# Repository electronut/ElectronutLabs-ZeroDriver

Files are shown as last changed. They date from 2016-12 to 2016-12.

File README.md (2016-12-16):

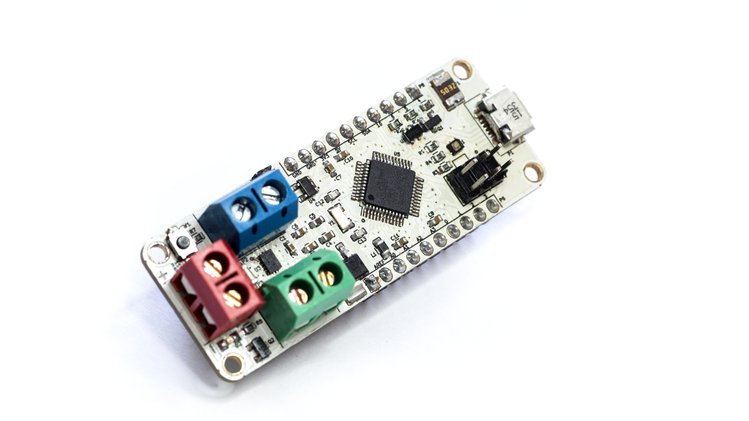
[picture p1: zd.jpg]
ZeroDriver


## What is it?

**ZeroDriver** is an Arduino Zero-compatible dual-motor driver board for robotics and mechatronics projects.

Robotics projects usually need two boards - a microcontroller board and a separate driver for the motors. ZeroDriver combines both in one for your convenience.

## Features & Specifications

* Atmel SAM D21 ARM Cortex-M0+ 48 MHz chip with 256KB Flash and 32KB SRAM
* Texas Instruments DRV8835 Dual Low-Voltage H-Bridge IC
* RGB LED
* Color coded terminal blocks for easy connectivity
* Standard 10-pin JTAG header broken out
* SPI header broken out
* Reverse polarity protection for power supply
* 12 V max power supply, 1.5 A current per H bridge
* Shipped with Arduino Zero bootloader for easy programming

## What can you do with it?

Well, depends on your imagination. :-)

But we do have some awesome demo projects - complete with code and design
information. Take a look at the [code](code/) directory.

## ZeroDriver Crowdfunding

We are currently trying to crowdfund the production of ZeroDriver at **Crowd Supply**.
Help us bring ZeroDriver to life!

https://www.crowdsupply.com/electronut-labs/zerodriver

## License

The following licenses apply to this work:

### Design Files

<br /><span xmlns:dct="http://purl.org/dc/terms/" property="dct:title">ZeroDriver</span> is licensed under a <a rel="license" href="http://creativecommons.org/licenses/by-sa/4.0/">Creative Commons Attribution-ShareAlike 4.0 International License</a>.<br />Based on a work at <a xmlns:dct="http://purl.org/dc/terms/" href="http://electronut.in/" rel="dct:source">http://electronut.in/</a>.

### Pin Diagram
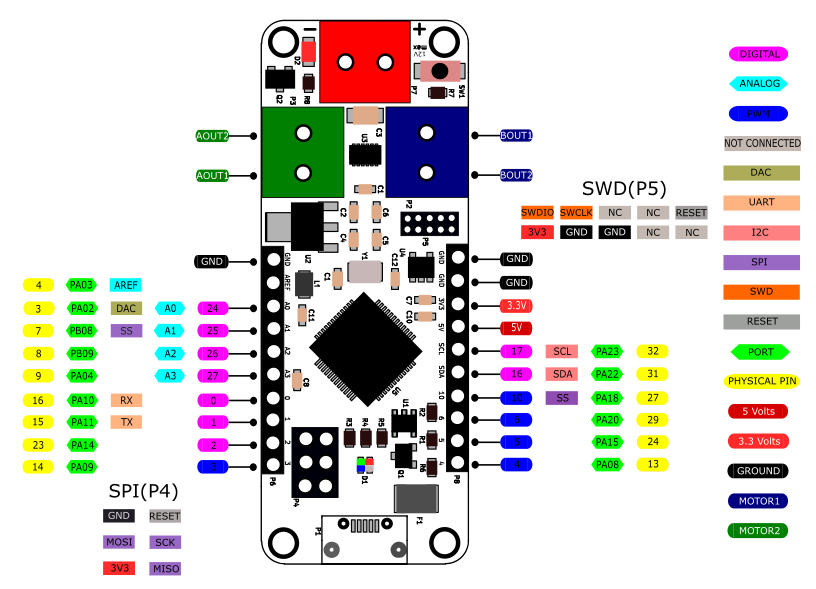
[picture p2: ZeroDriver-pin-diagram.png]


[Pinout](zerodriver-board-pinout.svg)
### Code

The MIT License (MIT)
Copyright (c) 2016 Electronut Labs (electronut.in)

Permission is hereby granted, free of charge, to any person obtaining a copy of this software and associated documentation files (the "Software"), to deal in the Software without restriction, including without limitation the rights to use, copy, modify, merge, publish, distribute, sublicense, and/or sell copies of the Software, and to permit persons to whom the Software is furnished to do so, subject to the following conditions:

The above copyright notice and this permission notice shall be included in all copies or substantial portions of the Software.

THE SOFTWARE IS PROVIDED "AS IS", WITHOUT WARRANTY OF ANY KIND, EXPRESS OR IMPLIED, INCLUDING BUT NOT LIMITED TO THE WARRANTIES OF MERCHANTABILITY, FITNESS FOR A PARTICULAR PURPOSE AND NONINFRINGEMENT. IN NO EVENT SHALL THE AUTHORS OR COPYRIGHT HOLDERS BE LIABLE FOR ANY CLAIM, DAMAGES OR OTHER LIABILITY, WHETHER IN AN ACTION OF CONTRACT, TORT OR OTHERWISE, ARISING FROM, OUT OF OR IN CONNECTION WITH THE SOFTWARE OR THE USE OR OTHER DEALINGS IN THE SOFTWARE.

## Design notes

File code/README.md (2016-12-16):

This directory consists of instructions and sample code for the examples developed using ZeroDriver.

**ZeroDriver-init** demonstrates the use of RGB LED and DRV8835 motor driver.

**Ultrasonic-bot** is an example of controlling DC motors i.e. their speed and direction using an ultrasonic sensor.

**Laser-step-test** demonstrates the ability of DC motors to generate various patterns using a laser pointer.

**Load-control** demonstrates the capability of DRV8835 is not only limited to control motors, but also in controlling and switching loads connected to the terminal blocks.

**stepper-iris** example explains the interfacing of a bipolar stepper motor with ZeroDriver. To make things interesting, an ultrasonic sensor controls the stepper motor to drive a mechanical iris.

**MeArm-joystick** demonstrates that MeArm - a robotic arm, can be controlled manually using two joysticks interfaced with the ZeroDriver.

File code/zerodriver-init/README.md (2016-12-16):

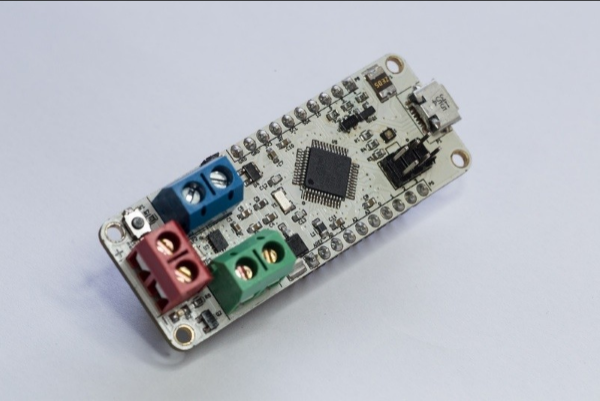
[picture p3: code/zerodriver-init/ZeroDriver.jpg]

#####ZeroDriver

Code to test RGB LED and DRV8835.

Plug in the USB to the ZeroDriver board and upload the code.

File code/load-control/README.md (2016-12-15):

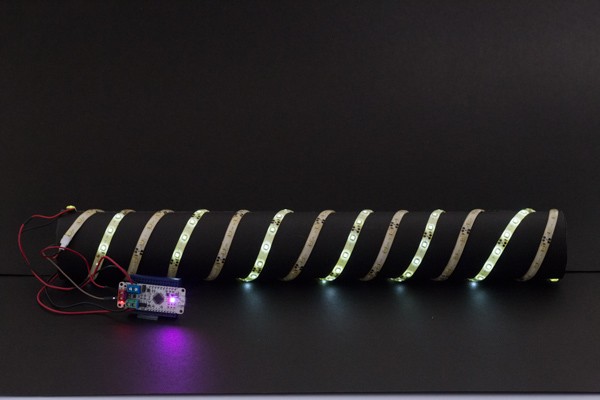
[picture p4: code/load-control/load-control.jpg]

#####LED strip control using H-bridges.

Two LED strips are connected to two H-bridges of the DRV8835. The RGB LED switches between _cyan_ and _magenta_ in accordance to the LED strip.

###Connections:
**LED strip** | **ZeroDriver**
--------- | ----------
VCC (LED strip 1) | AOUT1(+) Green terminal
GND (LED strip 1) | AOUT2(-) Green terminal
VCC (LED strip 2) | BOUT1(+) Blue terminal
GND (LED strip 2) | BOUT2(-) Blue terminal

_Note:_
Power ZeroDriver as per the ratings of the LED strip. Do not cross the max 12V input limit. Here, the board is powered with a 7.4V, 1300mAh LiPo battery.

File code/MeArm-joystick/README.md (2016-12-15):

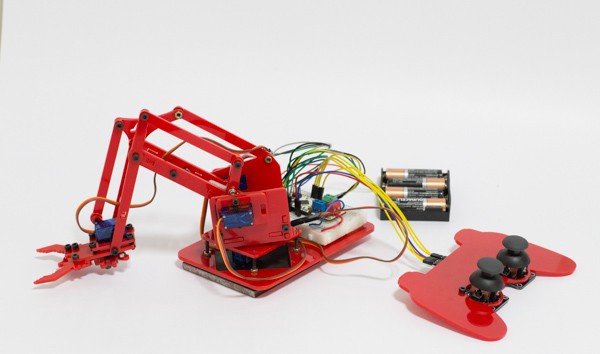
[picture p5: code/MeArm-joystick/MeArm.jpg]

#####Joystick interface with ZeroDriver to control [MeArm](https://mime.co.uk/products/mearm/).

The design files for MeARM are available at the link mentioned above. 
Design file for the joystick pad has been inuded in the repository.

###Connections:
**Joystick** | **ZeroDriver**
-------- | ----------
VCC | 3V3
XPOS (left joystick) | A0
YPOS (left joystick) | A1
XPOS (right joystick) | A2
YPOS (right joystick) | A3

**Servo Motors** | **ZeroDriver**
------------ | ----------
Base | 4
Left | 5
Right | 6
Claw | 10

_Note:_
Power the servo motors from 4 x AA batteries.

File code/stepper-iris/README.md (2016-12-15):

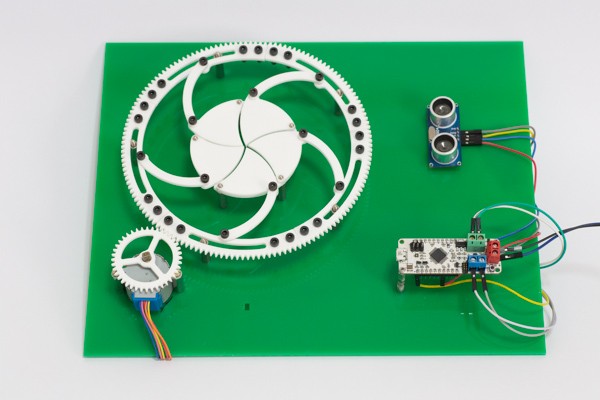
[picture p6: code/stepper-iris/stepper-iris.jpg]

#####Mechanical iris control using ultrasonic sensor and stepper motor

Controlling a mechanical iris using a stepper motor and an ultrasonic sensor. On detecting an object, the gear mounted stepper motor rotates, causing the iris to open. On removing the object, the iris is closed.

The iris design is based on a project - [Make an Awesome Mechanical Iris](http://makezine.com/projects/mechanical-iris/) by [Chris Schaie](http://makezine.com/author/chris-schaie/) The iris design has been modified for this project and included in the repository.

###Connections:
**HCSR-04** | **ZeroDriver**
------- | ----------
VCC | 5V
trigger | 2
echo | 4

**Stepper motor** | **ZeroDriver**
------------- | ----------
Blue | BOUT2(-) Blue terminal
Pink | AOUT2(-) Green terminal
Yellow | BOUT1(+) Blue terminal
Orange | AOUT(+) Green terminal

_Note:_

* The BYJ-48 is being used as a bipolar stepper motor in this demonstration. Do not connect the red wire of stepper motor. 
* HCSR-04 operates only when supplied with 5V. On powering with 3.3V, the sensor does not behave in a reliable manner. Naturally, on powering the sensor with 5V, the echo pin sends out 5V signals to the input pin 5 which can damage the board as the I/O pins are 3.3V compatible. Use a resistor divider network to generate 3.3V output from 5V echo signals.

###Reference:
https://itp.nyu.edu/physcomp/labs/motors-and-transistors/lab-controlling-a-stepper-motor-with-an-h-bridge/

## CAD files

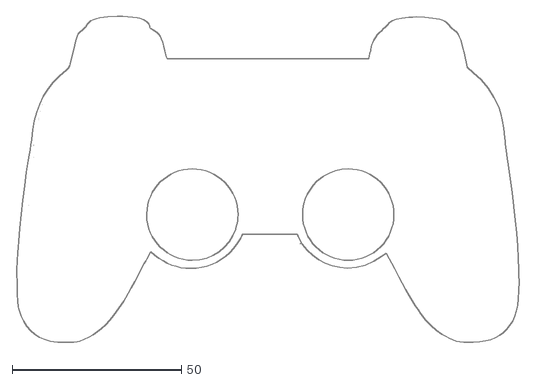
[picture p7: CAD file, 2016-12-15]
code/MeArm-joystick/Electronut-Labs-Joystick-board.dxf
148.8 x 96.6

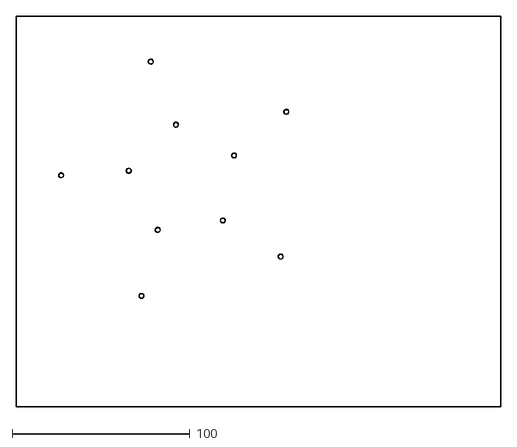
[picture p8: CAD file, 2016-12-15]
code/stepper-iris/Electronut-Labs-iris-frame.dxf
273.0 x 220.0

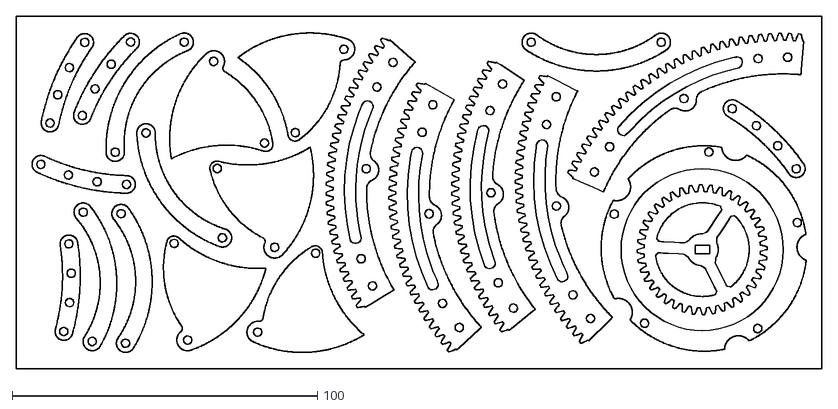
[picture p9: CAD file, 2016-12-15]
code/stepper-iris/Electronut-Labs-iris-parts.dxf
263.9 x 115.6

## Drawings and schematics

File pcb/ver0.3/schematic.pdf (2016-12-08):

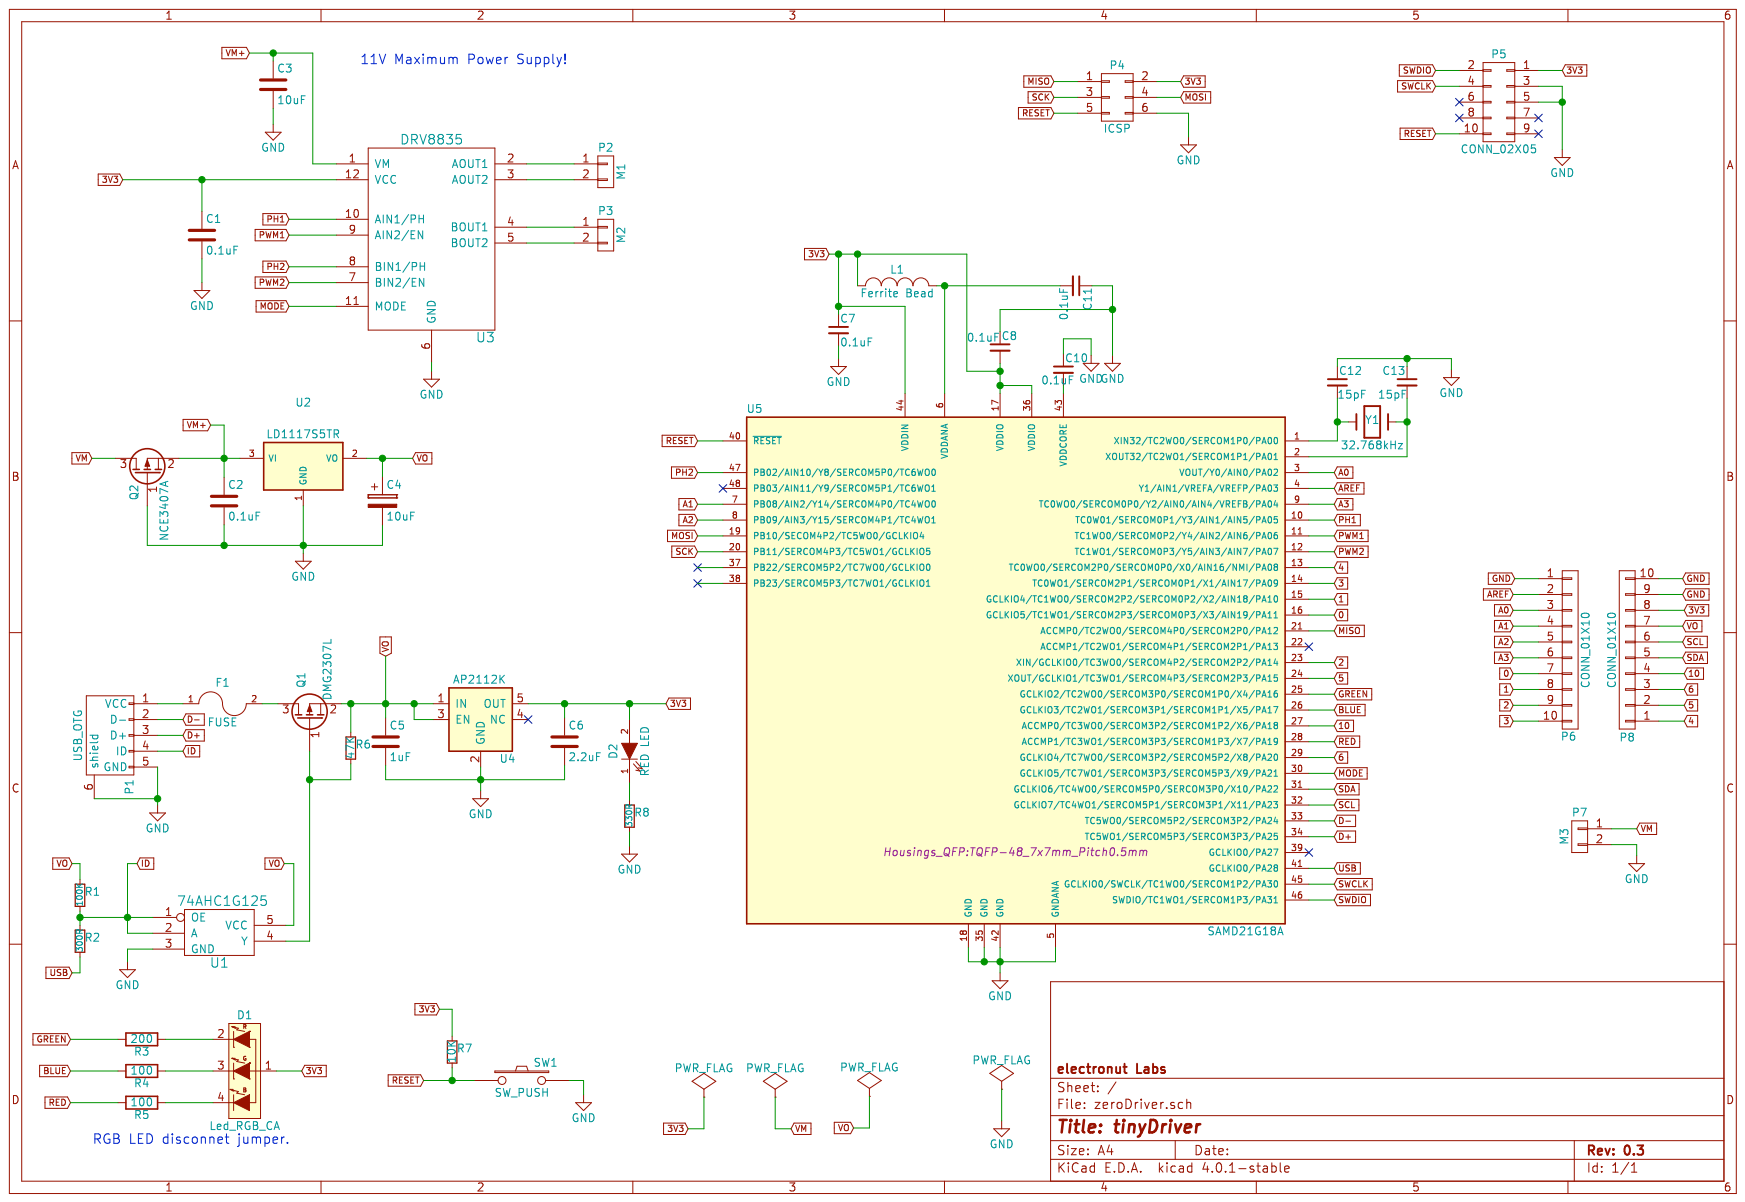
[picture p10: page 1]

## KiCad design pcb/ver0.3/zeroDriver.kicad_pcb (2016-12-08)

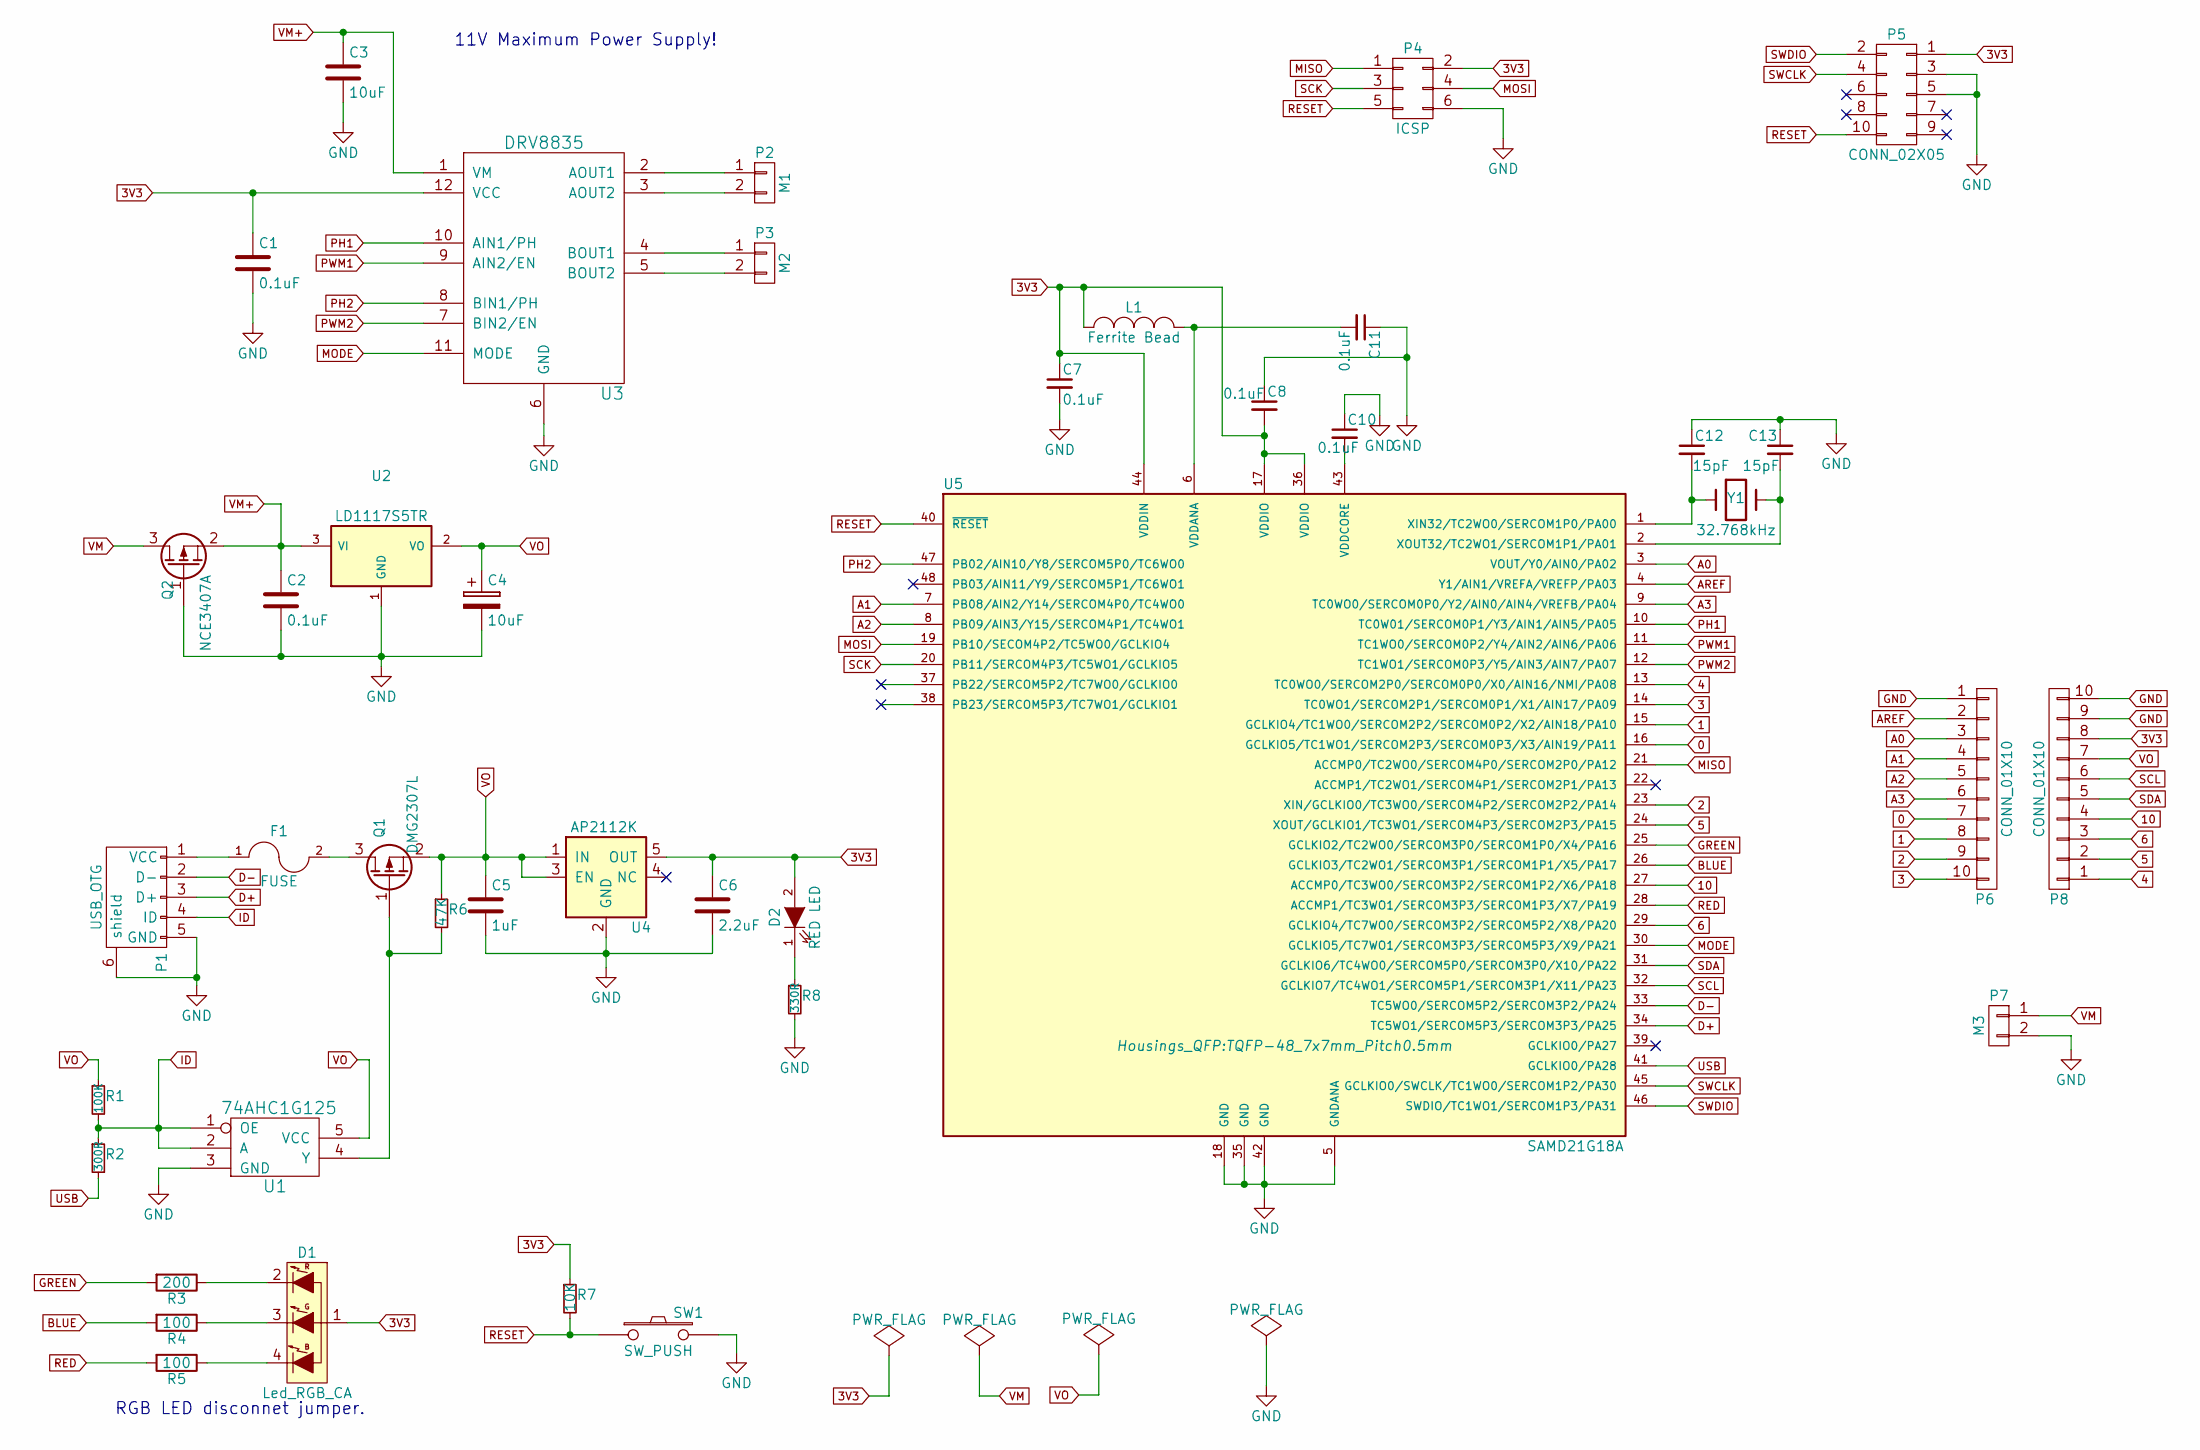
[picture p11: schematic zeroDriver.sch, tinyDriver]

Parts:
C1, C2, C7, C8, C10, C11: 0.1uF; C_0603
C3: 10uF; C_1206
C4: 10uF; C_0603
C5: 1uF; C_0603
C6: 2.2uF; C_0603
C12, C13: 15pF; C_0603
D1: Led_RGB_CA; CREE-CA
D2: RED LED; LED_0606
F1: FUSE; BOURNS_PTC_FUSE_S1
L1: Ferrite Bead; C_0805
P1: USB_OTG
P2: M1; TerminalBlock_5mm_1x2
P3: M2; TerminalBlock_5mm_1x2
P4: ICSP; ICSP_2x3
P5: CONN_02X05; JTAG
P6, P8: CONN_01X10; Pin_Header_Straight_1x10
P7: M3; TerminalBlock_5mm_1x2
Q1: DMG2307L; SOT-23
Q2: NCE3407A; SOT-23
R1: 100K; R_0603
R2: 300R; R_0603
R3: 200; R_0603
R4, R5: 100; R_0603
R6: 47K; R_0603
R7: 10K; R_0603
R8: 330R; R_0603
SW1: SW_PUSH; peter-switch
U1: 74AHC1G125; SOT-23-5
U2: LD1117S5TR; LD1117_SOT223
U3: DRV8835
U4: AP2112K; SOT-23-5
U5: SAMD21G18A; TQFP-48_7x7mm_Pitch0.5mm
Y1: 32.768kHz; crystal

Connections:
0: P6.7, U5.16 (GCLKIO5/TC1WO1/SERCOM2P3/SERCOM0P3/X3/A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)
1: P6.8, U5.15 (GCLKIO4/TC1WO0/SERCOM2P2/SERCOM0P2/X2/A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)
2: P6.9, U5.23 (XIN/GCLKIO0/TC3WO0/SERCOM4P2/SERCOM2P2/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)
3: P6.10, U5.14 (TC0WO1/SERCOM2P1/SERCOM0P1/X1/AIN17/PA09)
3V3: C1.1, C6.1, C7.1, C8.2, D1.1, D2.2 (A), L1.1, P4.2, P5.1, P8.8, R7.1, U3.12 (VCC), U4.5 (OUT), U5.17 (VDDIO), U5.36 (VDDIO), U5.44 (VDDIN)
4: P8.1, U5.13 (TC0WO0/SERCOM2P0/SERCOM0P0/X0/AIN16/NMI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)
5: P8.2, U5.24 (XOUT/GCLKIO1/TC3WO1/SERCOM4P3/SERCOM2P3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)
6: P8.3, U5.29 (GCLKIO4/TC7WO0/SERCOM3P2/SERCOM5P2/X8/P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)
10: P8.4, U5.27 (ACCMP0/TC3WO0/SERCOM3P2/SERCOM1P2/X6/PA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)
A0: P6.3, U5.3 (VOUT/Y0/AIN0/PA02)
A1: P6.4, U5.7 (PB08/AIN2/Y14/SERCOM4P0/TC4WO0)
A2: P6.5, U5.8 (PB09/AIN3/Y15/SERCOM4P1/TC4WO1)
A3: P6.6, U5.9 (TC0WO0/SERCOM0P0/Y2/AIN0/AIN4/VREFB/PA04)
AREF: P6.2, U5.4 (Y1/AIN1/VREFA/VREFP/PA03)
BLUE: R4.2, U5.26 (GCLKIO3/TC2WO1/SERCOM3P1/SERCOM1P1/X5/P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)
D+: P1.3 (D+), U5.34 (TC5WO1/SERCOM5P3/SERCOM3P3/PA25)
D-: P1.2 (D-), U5.33 (TC5WO0/SERCOM5P2/SERCOM3P2/PA24)
GND: C1.2, C2.2, C3.2, C4.2, C5.2, C6.2, C7.2, C8.1, C10.1, C11.1, C12.1, C13.1, P1.5 (GND), P1.6 (shield), P4.6, P5.3, P5.5, P6.1, P7.2, P8.9, P8.10, Q2.1 (G), R8.2, SW1.2, U1.3 (GND), U2.1 (GND), U3.6 (GND), U4.2 (GND), U5.5 (GNDANA), U5.18 (GND), U5.35 (GND), U5.42 (GND)
GREEN: R3.2, U5.25 (GCLKIO2/TC2WO0/SERCOM3P0/SERCOM1P0/X4/P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)
ID: P1.4 (ID), R1.2, R2.1, U1.1 (OE), U1.2 (A)
MISO: P4.1, U5.21 (ACCMP0/TC2WO0/SERCOM4P0/SERCOM2P0/PA12)
MODE: U3.11 (MODE), U5.30 (GCLKIO5/TC7WO1/SERCOM3P3/SERCOM5P3/X9/P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)
MOSI: P4.4, U5.19 (PB10/SECOM4P2/TC5WO0/GCLKIO4)
unnamed: C10.2, U5.43 (VDDCORE)
unnamed: C11.2, L1.2, U5.6 (VDDANA)
unnamed: C12.2, U5.1 (XIN32/TC2WO0/SERCOM1P0/PA00), Y1.1
unnamed: C13.2, U5.2 (XOUT32/TC2WO1/SERCOM1P1/PA01), Y1.2
unnamed: D1.2 (R), R3.1
unnamed: D1.3 (G), R4.1
unnamed: D1.4 (B), R5.1
unnamed: D2.1 (K), R8.1
unnamed: F1.1, P1.1 (VCC)
unnamed: F1.2, Q1.3 (D)
unnamed: P2.1, U3.2 (AOUT1)
unnamed: P2.2, U3.3 (AOUT2)
unnamed: P3.1, U3.4 (BOUT1)
unnamed: P3.2, U3.5 (BOUT2)
unnamed: Q1.1 (G), R6.2, U1.4 (Y)
PH1: U3.10 (AIN1/PH), U5.10 (TC0W01/SERCOM0P1/Y3/AIN1/AIN5/PA05)
PH2: U3.8 (BIN1/PH), U5.47 (PB02/AIN10/Y8/SERCOM5P0/TC6WO0)
PWM1: U3.9 (AIN2/EN), U5.11 (TC1WO0/SERCOM0P2/Y4/AIN2/AIN6/PA06)
PWM2: U3.7 (BIN2/EN), U5.12 (TC1WO1/SERCOM0P3/Y5/AIN3/AIN7/PA07)
RED: R5.2, U5.28 (ACCMP1/TC3WO1/SERCOM3P3/SERCOM1P3/X7/PA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)
RESET: P4.5, P5.10, R7.2, SW1.1, U5.40 (~RESET~)
SCK: P4.3, U5.20 (PB11/SERCOM4P3/TC5WO1/GCLKIO5)
SCL: P8.6, U5.32 (GCLKIO7/TC4WO1/SERCOM5P1/SERCOM3P1/X11/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)
SDA: P8.5, U5.31 (GCLKIO6/TC4WO0/SERCOM5P0/SERCOM3P0/X10/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)
SWCLK: P5.4, U5.45 (GCLKIO0/SWCLK/TC1WO0/SERCOM1P2/PA30)
SWDIO: P5.2, U5.46 (SWDIO/TC1WO1/SERCOM1P3/PA31)
USB: R2.2, U5.41 (GCLKIO0/PA28)
VM: P7.1, Q2.3 (D)
VM+: C2.1, C3.1, Q2.2 (S), U2.3 (VI), U3.1 (VM)
VO: C4.1, C5.1, P8.7, Q1.2 (S), R1.1, R6.1, U1.5 (VCC), U2.2 (VO), U4.1 (IN), U4.3 (EN)

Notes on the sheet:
RGB LED disconnet jumper.
11V Maximum Power Supply!

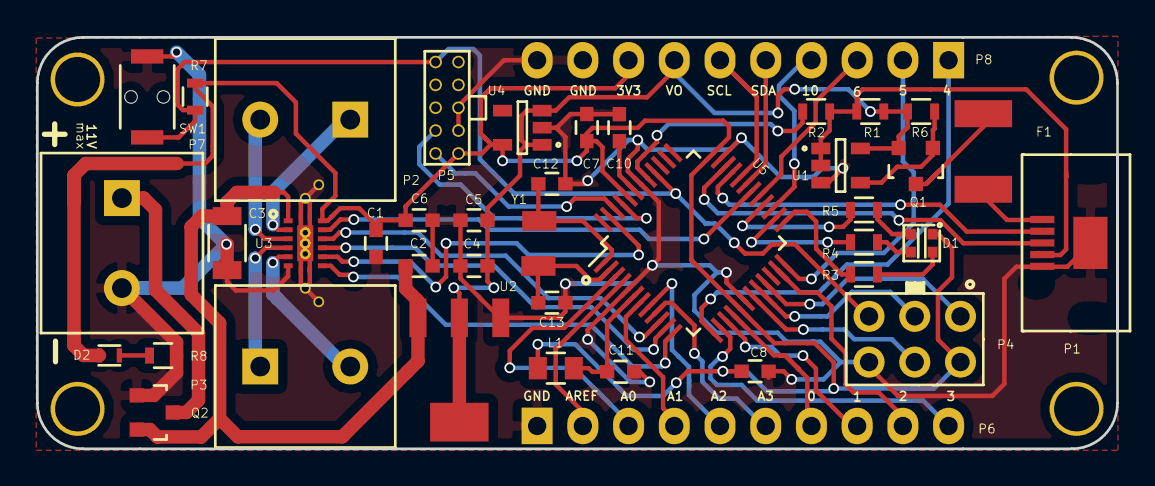
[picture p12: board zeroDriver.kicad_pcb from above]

Board: 2 copper layers, 60.0 x 22.9 mm, 48 parts (1 on the bottom side), 53 nets.

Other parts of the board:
via: VAL**; via
via#2, via#3, via#4, via#5, via#6, via#7: VAL**; via

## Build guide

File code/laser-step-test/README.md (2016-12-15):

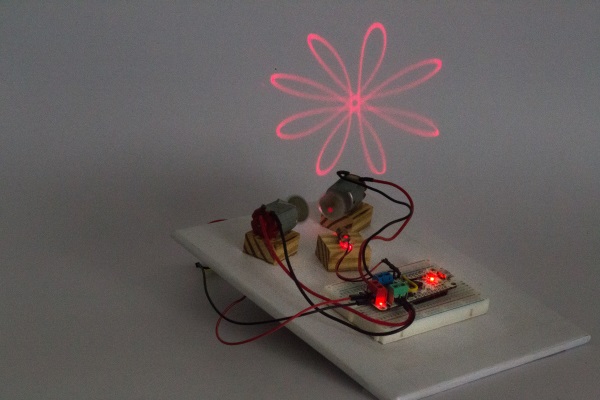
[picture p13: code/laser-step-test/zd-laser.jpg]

#####Patterns from a laser module and spinning motors.

Varying patterns can be generated by shining a laser beam mounted on two motors spinning at varying speed.
`random()` function is used to generate varying PWM values for the motors at an interval of 5 seconds.
Also, the motors are programmed to switch directions simultaneously. This is indicated by the switching of RGB LED between cyan and magenta colors.

###Connections:
**Motors** | **ZeroDriver**
------ | ----------
Red wire (motor1) | AOUT2(-) Green terminal
Black wire (motor1) | AOUT1(+) Green terminal
Red wire (motor2) | BOUT1(+) Blue terminal
Black wire (motor2) | BOUT2(-) Blue terminal

* The [Laser module](http://www.dx.com/p/6mm-5mw-red-laser-module-3-5-4-5v-13378#.WE-xKPl9602) has a 22 ohm resistor soldered to it and connected to 5V pin on the board.

_Note:_

Spin the motors in same and opposite direction to achieve varying patterns.

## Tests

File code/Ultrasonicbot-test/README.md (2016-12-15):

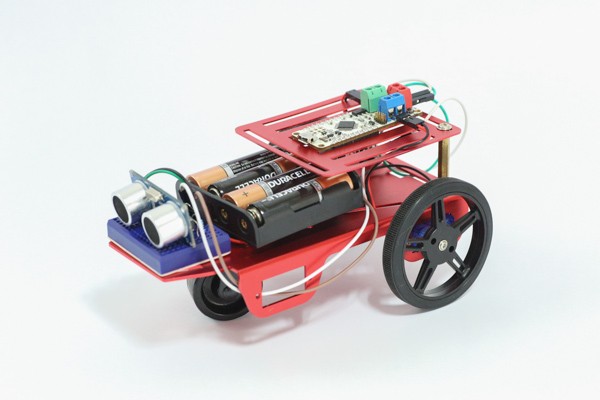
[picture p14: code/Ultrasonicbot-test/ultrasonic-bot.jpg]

######ZeroDriver based object detecting 2 wheel bot. 

The Ultrasonic bot is an object detecting 2 wheel bot. The bot moves in a straight path unless obstructed with an object. If the bot detects an object within a range of 10 cms, it halts and reverses for a short distance. This is followed by a left turn to change the bot's trajectory. The RGB LED on ZeroDriver signifies various motions of the bot i.e 

###Connections:
**HCSR-04** | **ZeroDriver**
------- | ----------
VCC | 5V
trigger | 2
echo | 5

* Connect DC motors to green and blue terminal blocks.

_Note:_ 
HCSR-04 operates only when supplied with 5V. On powering with 3.3V, the sensor does not behave in a reliable manner. Naturally, on powering the sensor with 5V, the echo pin sends out 5V signals to the input pin 5 which can damage the board as the I/O pins are 3.3V compatible. Use a resistor divider network to generate 3.3V output from 5V echo signals.

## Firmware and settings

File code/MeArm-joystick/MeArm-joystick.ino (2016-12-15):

/*
 * MeArm Joystick - This example demonstrates the working of MeArm robotic arm
   using ZeroDriver. The MeArm is controlled using two joysticks. 
    
 * Reference: https://codebender.cc/sketch:169809#MeArm_Joy_NoLCD.ino
 
 * Author : Electronut Labs
 * Website  : electronut.in
*/

#include <Servo.h> 

#define XPOS 0
#define YPOS 1

const int SERVOS = 4;
const int ACC = 10; // the accurancy of the potentiometer value before idle starts counting
int PIN[SERVOS], value[SERVOS], idle[SERVOS], currentAngle[SERVOS], MIN[SERVOS], MAX[SERVOS], INITANGLE[SERVOS], previousAngle[SERVOS],ANA[SERVOS];
Servo myservo[SERVOS];

void setup()   {
  SerialUSB.begin(57600);
  //Middle Servo
  PIN[0] = 4;
  MIN[0] = 0;
  MAX[0] = 180;
  INITANGLE[0] = 90;
  ANA[0] = 1;
  //Left Side
  PIN[1] = 5;
  MIN[1] = 20;
  MAX[1] = 170;
  INITANGLE[1] = 45;
  ANA[1] = 0;
  //Right Side
  PIN[2] = 6;
  MIN[2] = 30;
  MAX[2] = 150;
  INITANGLE[2] = 60;
  ANA[2] = 2;
  //Claw Servo
  PIN[3] = 10;
  MIN[3] = 0;
  MAX[3] = 80;
  INITANGLE[3] = 25;
  ANA[3] = 3;
  
  for (int i = 0; i < SERVOS; i++) {
    myservo[i].attach(PIN[i]);
    myservo[i].write(INITANGLE[i]);
    value[i] = 0;
    idle[i] = 0;
    previousAngle[i]=INITANGLE[i];
  }
}

void loop() {
  // Delay function to slow movement of arm down
  delay(15); 
  for (int i = 0; i < SERVOS; i++) {
    // read analog values from joysticks.
    value[i] = analogRead(ANA[i]); 
    // read current position of each servo.
    currentAngle[i] = myservo[i].read();
  
    if (value[i] > 612) {
      idle[i] = 0;
      // if current position less than maximum position, increment position.
      if (currentAngle[i] < MAX[i]) 
        ++currentAngle[i];
      if (!myservo[i].attached()) {
        myservo[i].attach(PIN[i]);
      }
      // set servos to the desired position.
      myservo[i].write(currentAngle[i]);     
    } 
    else if (value[i] < 412) {
      idle[i] = 0;
      // if current position greater than maximum position, decrement position.
      if (currentAngle[i] > MIN[i]) --currentAngle[i];
      if (!myservo[i].attached()) {
        myservo[i].attach(PIN[i]);
      }
      // set servos to the desired position.
      myservo[i].write(currentAngle[i]);    
    } 
    else {
      ++idle[i];
    }
    if (idle[i] > 100) {
      myservo[i].detach();
      idle[i] = 0;
    }  
  }  
}

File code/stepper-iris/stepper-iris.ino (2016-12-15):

/*
 * Stepper-Iris - This example demonstrates the movement of a mechanical iris using a Stepper motor 
   and an Ultrasonic sensor. On detecting an object in front of the sensor, the gear mounted stepper
   motor rotates, causing the iris to open. On removing the object, the iris is closed.  
    
 * Author : Electronut Labs
 * Website  : electronut.in
*/
 
#include <Stepper.h>

// number of steps required for the internal gear to complete one rotation
#define stepsPerRevolution 32
// number of steps required for external shaft to complete one rotation.
#define stepsPerOutputRevolution 32*64

// HCSR-04 initialization.
int trigger = 2;
int echo = 4;

// gear ratio = T2/T1; where T1 is the number of teeth on drive gear (gear connected to motor) and T2 is the number of teeth on driven gear (gear connected to load).
// gear ratio determines the number of turns drive gear needs to make for the driven gear to achieve one complete rotation.
// T2 = 13 (to open or close the iris), T1 = 40.
// gear ratio = 13/40
// gear ratio = 0.325
// steps = 0.325 * stepsPerOutputRevolution
// steps = 665.6

int steps =  0.325 * stepsPerOutputRevolution;

// initialize the stepper library.
Stepper myStepper(stepsPerRevolution, A5, 9, A4, 8);

float getDistance()
{
  // send a 10uS pulse
  digitalWrite(trigger, LOW);
  delayMicroseconds(20);
  digitalWrite(trigger, HIGH);
  delayMicroseconds(10);
  digitalWrite(trigger, LOW);
  delayMicroseconds(20);

  //echo duration
  int duration = pulseIn(echo, HIGH);

  if(duration > 0) {
    // dist = duration * speed of sound * 0.5
    // dist in cm = duration in uS * 10^(-6) * 340.26 * 100 * 0.5
    // = duration * 0.017
    float dist = duration * 0.017;
    //SerialUSB.println(dist);
    return dist;
  }
}

void stopStepper()
{
  digitalWrite(9, LOW);
  digitalWrite(8, LOW);
}

int R = 12;
int G = 11;
int B = 13;

void flashRed()
{
  // red ON  
  digitalWrite(R, LOW);
  digitalWrite(G, HIGH);
  digitalWrite(B, HIGH);

  delay(1000);

  // LED OFF
  digitalWrite(R, HIGH);
  digitalWrite(G, HIGH);
  digitalWrite(B, HIGH);

  delay(1000);

  // red ON
  digitalWrite(R, LOW);
  digitalWrite(G, HIGH);
  digitalWrite(B, HIGH);

  delay(1000);

  // LED OFF
  digitalWrite(R, HIGH);
  digitalWrite(G, HIGH);
  digitalWrite(B, HIGH);
}

void setup() {
  // set the speed at 700 rpm:
  myStepper.setSpeed(700);
  // initialize the serial port:
  SerialUSB.begin(9600);

  // set HCSR-04 pins
  pinMode(trigger, OUTPUT);
  pinMode(echo, INPUT);

  stopStepper();

  // set RGB LED pins
  pinMode(R, OUTPUT);
  pinMode(G, OUTPUT);
  pinMode(B, OUTPUT);

  // blink Red twice.
  flashRed();
}

float currentDistance;
float previousDistance = 0.0;

bool flag = false;

void loop() {
  currentDistance = getDistance();

  // object detected
  if(currentDistance <= 15) {
    myStepper.step(steps);
    delay(500);
    flag = true;
  }
  // object removed
  if((currentDistance > 15) && (flag == true)) {
    myStepper.step(-steps);
    flag = false;
  }
  stopStepper();
}

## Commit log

2016-12-08 added pcb files
    [zeroDriver-B.Cu.gbl, zeroDriver-B.Mask.gbs, zeroDriver-B.Paste.gbp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]
2016-12-16 updated pin diagram
2016-12-16 pin diagram image added
